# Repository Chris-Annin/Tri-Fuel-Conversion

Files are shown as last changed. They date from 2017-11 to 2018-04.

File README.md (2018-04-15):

# Tri-Fuel-Conversion
open source instructions and 3D print models to convert your generator to run on natural gas or propane

This project includes:

- Bill of materials and instructions
- CAD files to 3D print bracket and carburetor adapter

(https://youtu.be/Tu0BFD9ouBQ)

Overview: [Video](https://youtu.be/Tu0BFD9ouBQ)

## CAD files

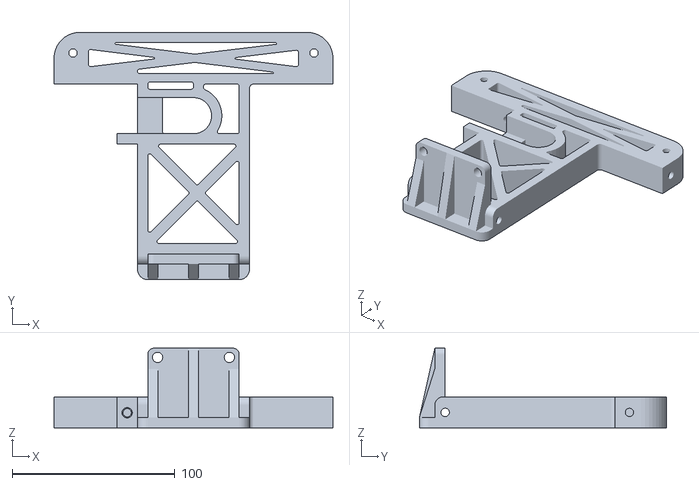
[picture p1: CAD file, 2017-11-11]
Mounting Bracket.STL
171.4 x 152.0 x 49.0

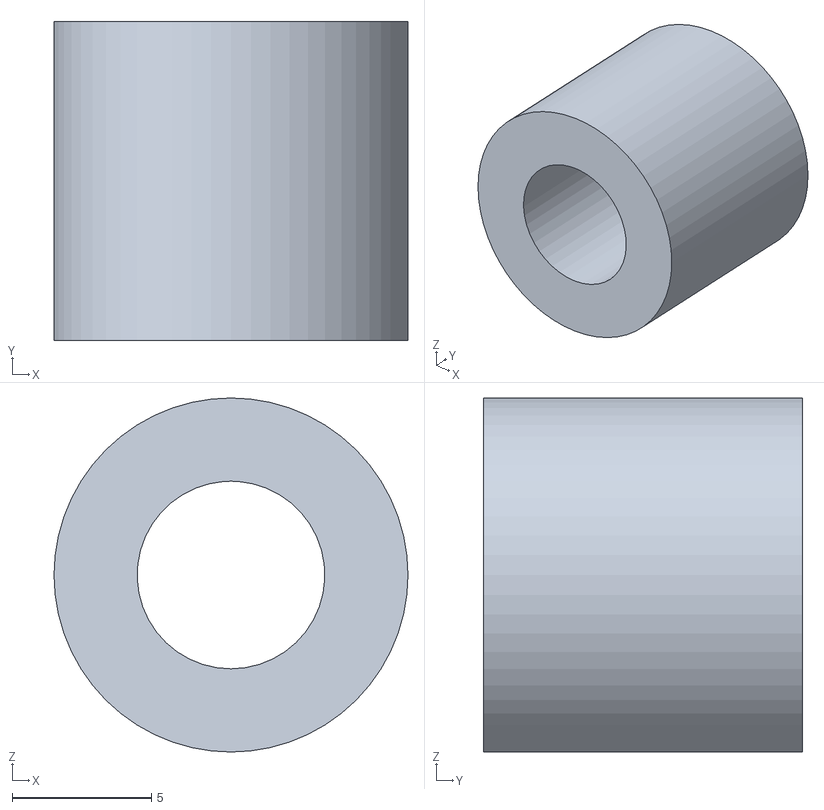
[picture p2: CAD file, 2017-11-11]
Lever Spacer.STL
12.7 x 11.4 x 12.7

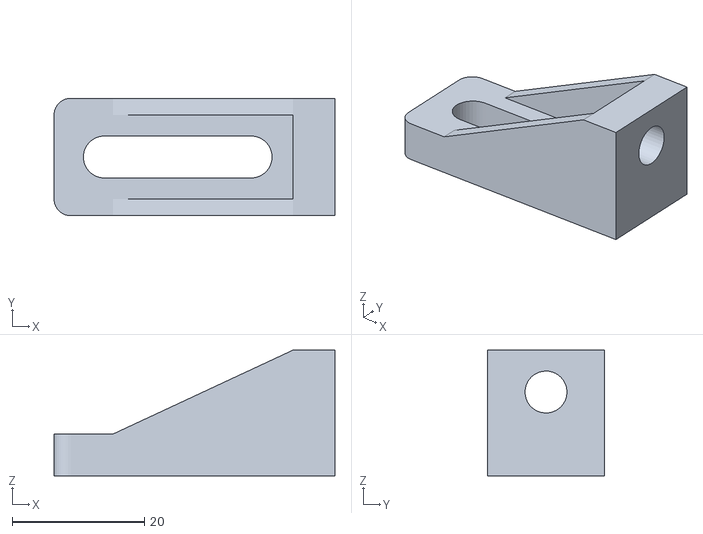
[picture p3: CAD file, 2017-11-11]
Foot.STL
42.5 x 17.8 x 19.1

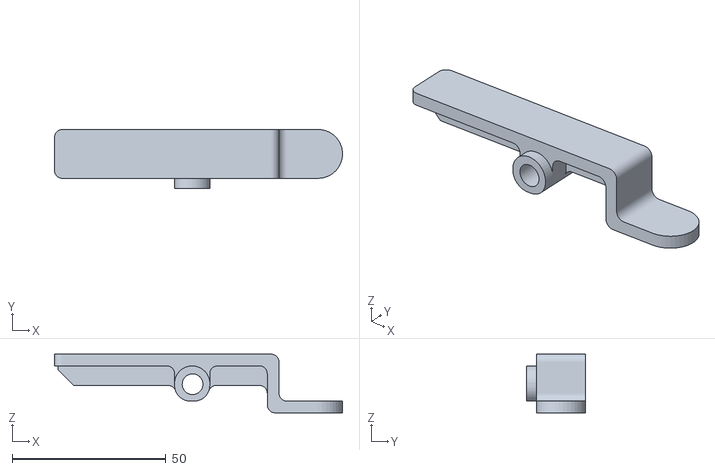
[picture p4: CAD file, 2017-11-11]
Lever.STL
93.5 x 19.2 x 19.1

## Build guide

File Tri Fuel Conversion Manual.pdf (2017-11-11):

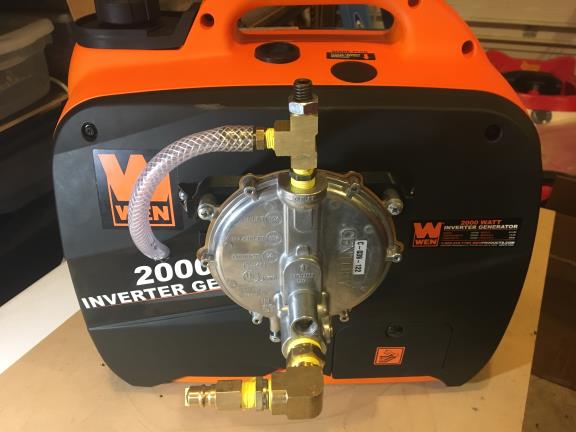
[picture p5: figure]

# Tri Fuel Conversion Manual

### - WARNING

- Never use a generator inside homes, garages,

### crawlspaces, or other partly enclosed areas. Deadly levels of carbon monoxide can build up in these areas. Using a fan or opening windows and doors

does NOT supply enough fresh air.

### - ONLY use a generator outdoors and far away from open windows, doors, and vents. Make sure to direct the generator's exhaust away from these openings because they can pull in generator

exhaust.

### - The generator must be at least 20 ft away from your

home.

- Before making any connections make sure you identify and eliminate all sources of ignition where natural gas may be vented, recognizing that natural gas is lighter than air and will rise. Sources of ignition include: - Standing pilots - Open flames - Cigarettes and other smoking products - Electric light switches and appliances - Motorized equipment and vehicles - Temperatures above 1,100 degrees Fahrenheit - Anything that may cause a spark - Use natural gas detection equipment during all natural gas or propane connection operations to prevent natural gas from accumulating and creating a combustible or hazardous atmosphere. DO NOT rely on your sense of smell alone to be alerted the

presence of natural gas.

# Bill of Materials

### ITEMS FROM AMAZON:

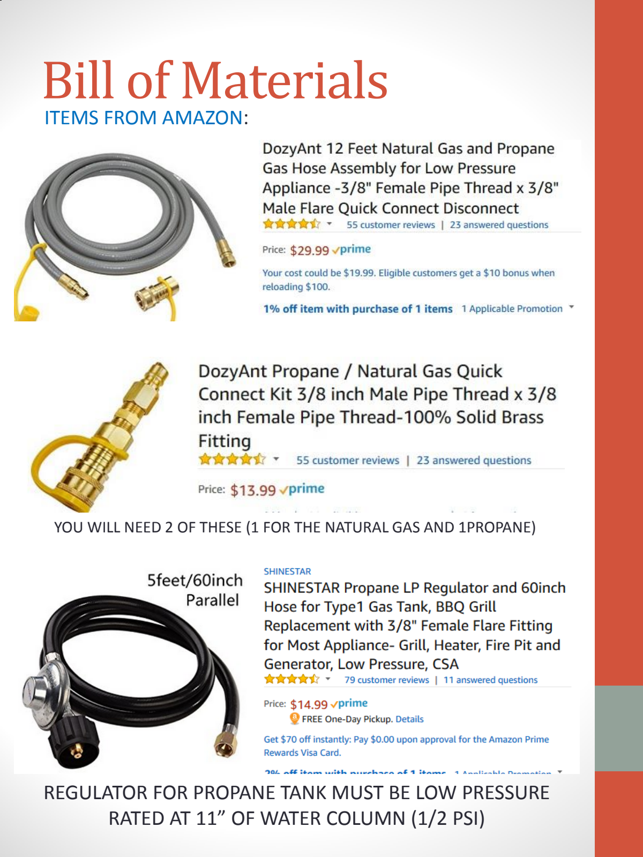
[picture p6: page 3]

YOU WILL NEED 2 OF THESE (1 FOR THE NATURAL GAS AND 1PROPANE)

### REGULATOR FOR PROPANE TANK MUST BE LOW PRESSURE RATED AT 11” OF WATER COLUMN (1/2 PSI)

### ITEMS FROM EBAY:

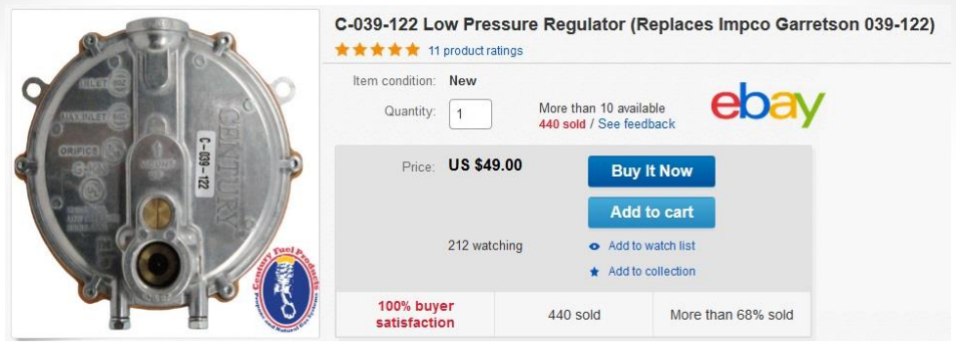
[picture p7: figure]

### ITEMS FROM HARDWARE STORE – GENERATOR FITTINGS:

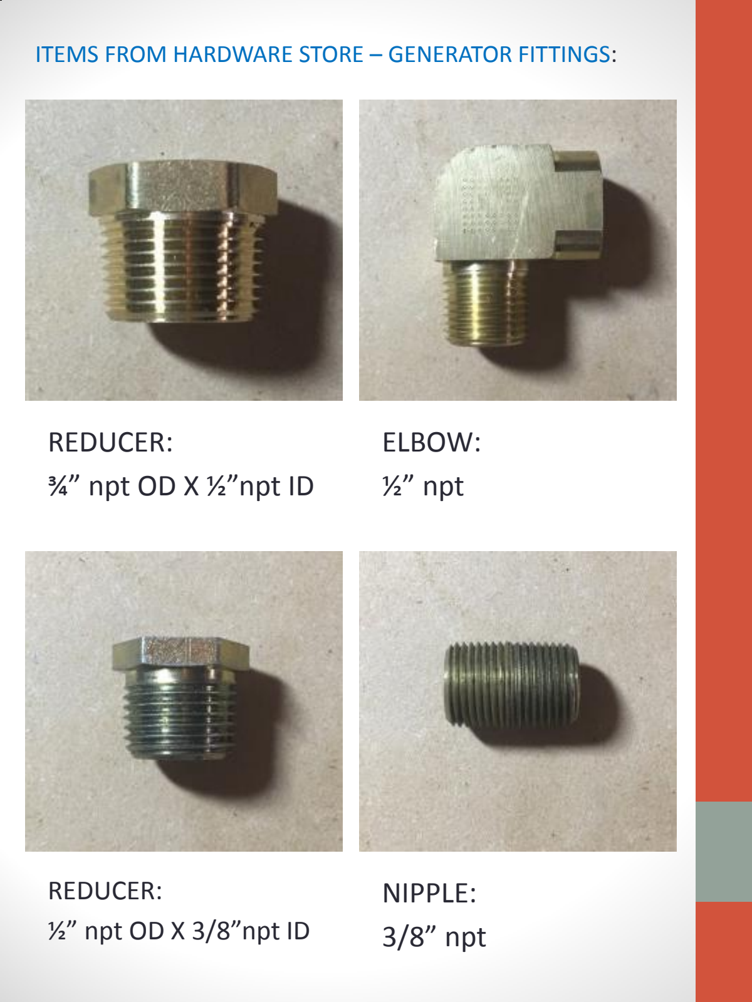
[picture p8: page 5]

## REDUCER: ¾” npt OD X ½”npt ID

## ELBOW: ½” npt

## REDUCER: ½” npt OD X 3/8”npt ID

## NIPPLE: 3/8” npt

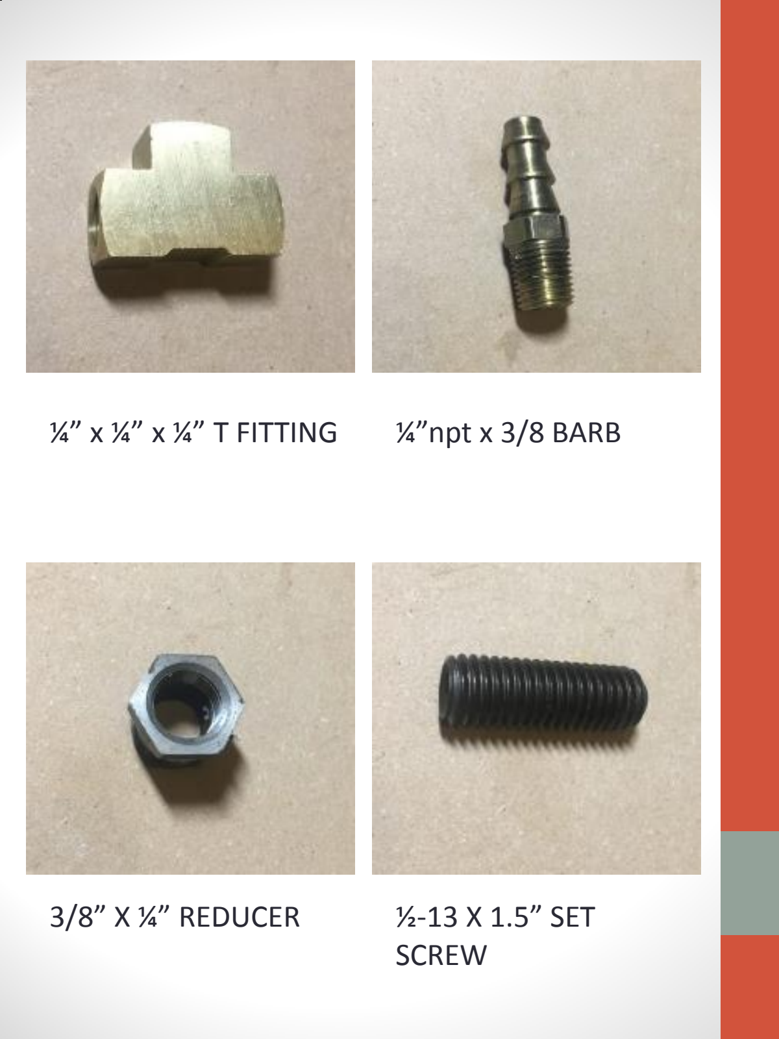
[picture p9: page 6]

3/8” X ¼” REDUCER | ½-13 X 1.5” SET SCREW
¼” x ¼” x ¼” T FITTING | ¼”npt x 3/8 BARB

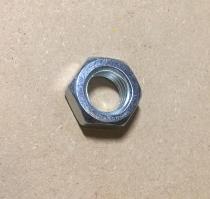
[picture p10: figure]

## ½-13 JAM NUT

## ¼” npt NIPPLE

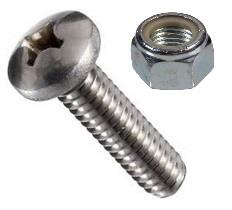
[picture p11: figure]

¼” x 1.75” machine screws (x1) ¼” x .5” machine screws (x8) ¼” X 1” machine screws (x2) ¼” nylon lock nuts (x4)

### ITEMS FROM HARDWARE STORE – NATURAL GAS SUPPLY:

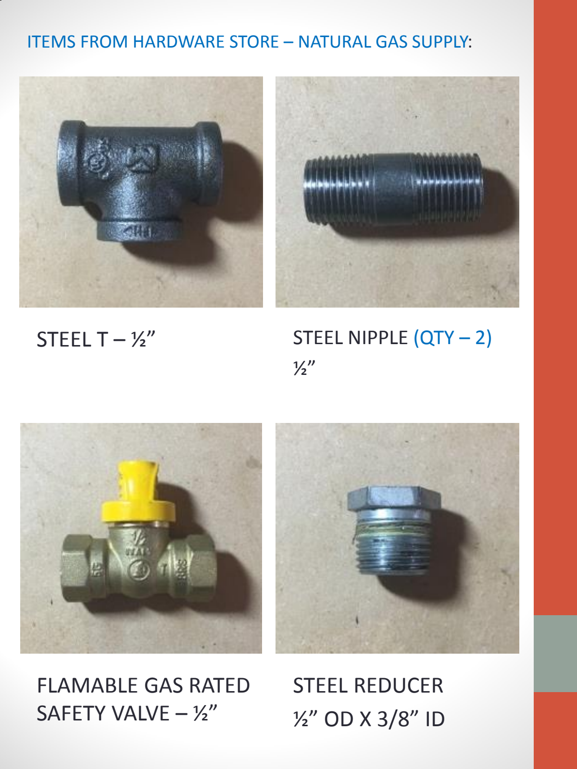
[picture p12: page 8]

STEEL T – ½” | STEEL NIPPLE (QTY – 2) ½”

## FLAMABLE GAS RATED SAFETY VALVE – ½”

## STEEL REDUCER ½” OD X 3/8” ID

## STEEL NIPPLE:

3/8”

## GAS RATED TEFLON TAPE

## FLARE FITTING: 3/8” FLARE X 3/8” npt

### ITEMS FROM HARDWARE STORE – PROPANE SUPPLY:

### 3D PRINTED PARTS

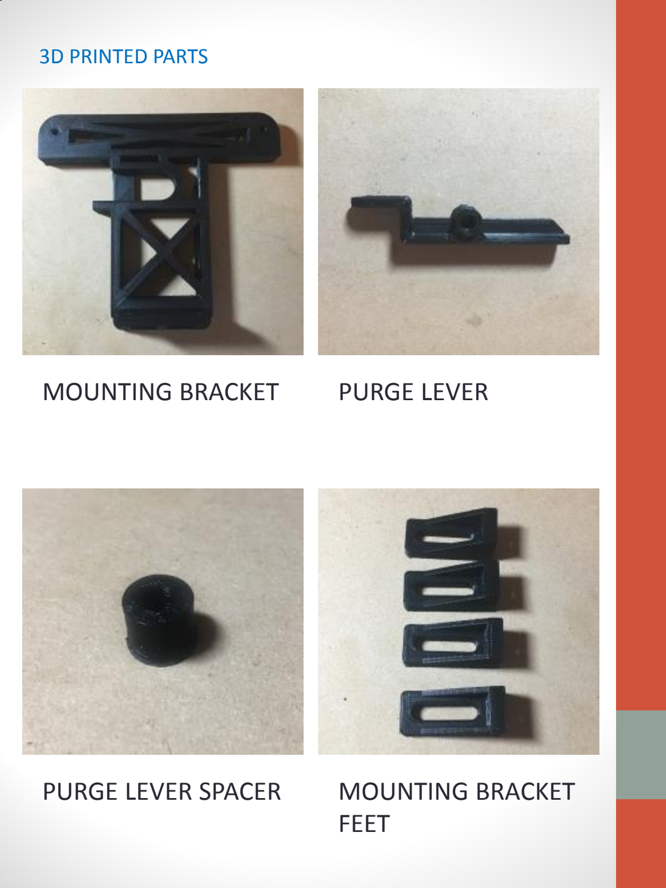
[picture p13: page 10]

MOUNTING BRACKET | PURGE LEVER
PURGE LEVER SPACER | MOUNTING BRACKET FEET

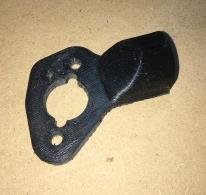
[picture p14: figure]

## CARBURATOR GAS ADAPTER

# Assembly

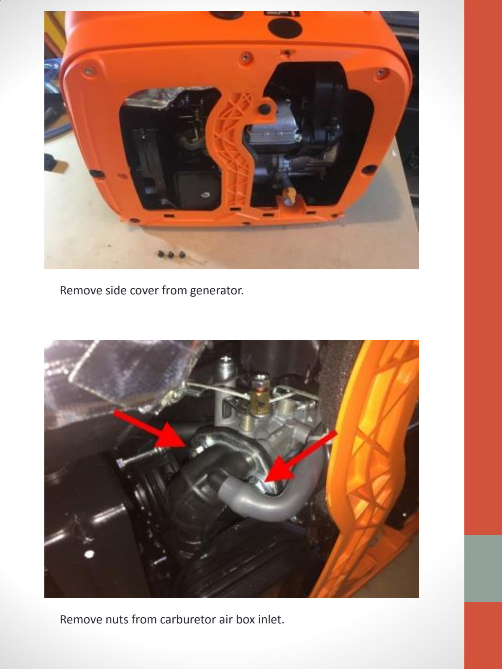
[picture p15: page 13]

Remove side cover from generator.

Remove nuts from carburetor air box inlet.

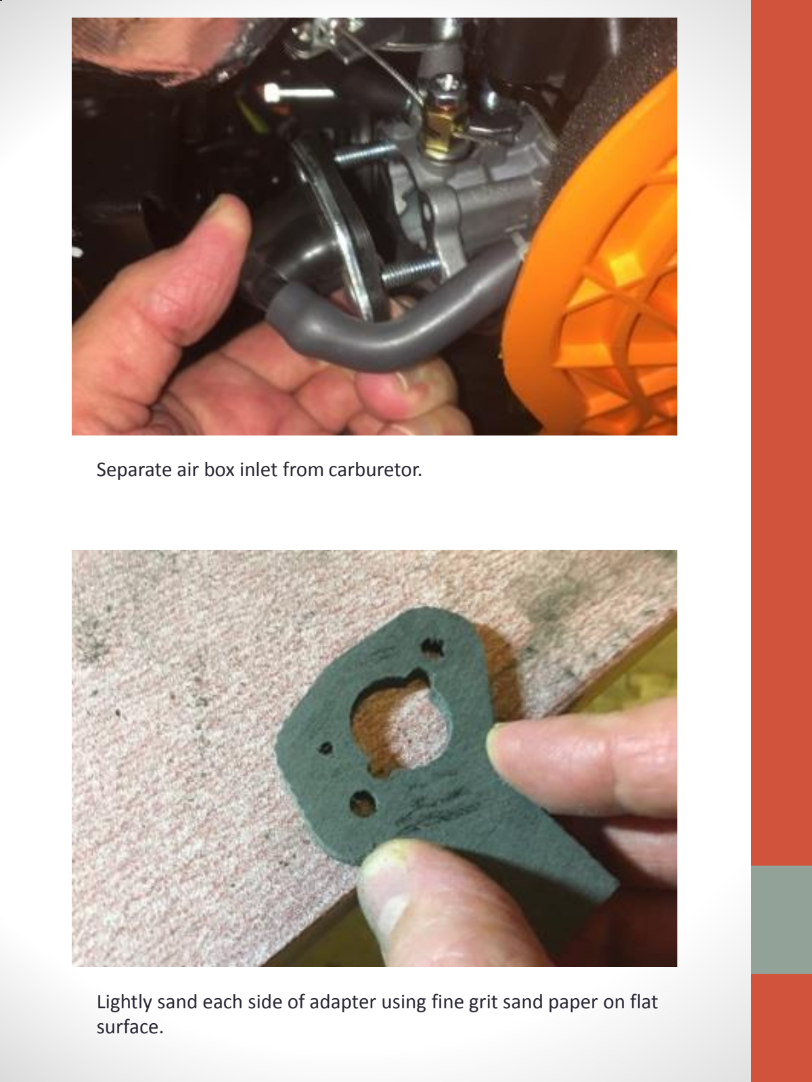
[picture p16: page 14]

Separate air box inlet from carburetor.

Lightly sand each side of adapter using fine grit sand paper on flat surface.

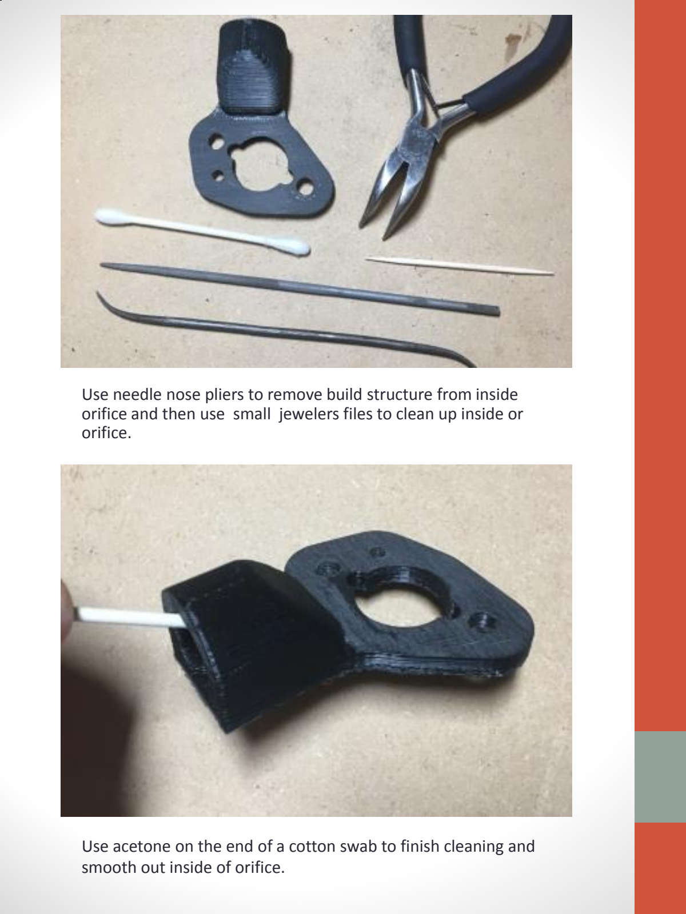
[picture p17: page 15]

Use needle nose pliers to remove build structure from inside orifice and then use small jewelers files to clean up inside or orifice.

Use acetone on the end of a cotton swab to finish cleaning and smooth out inside of orifice.

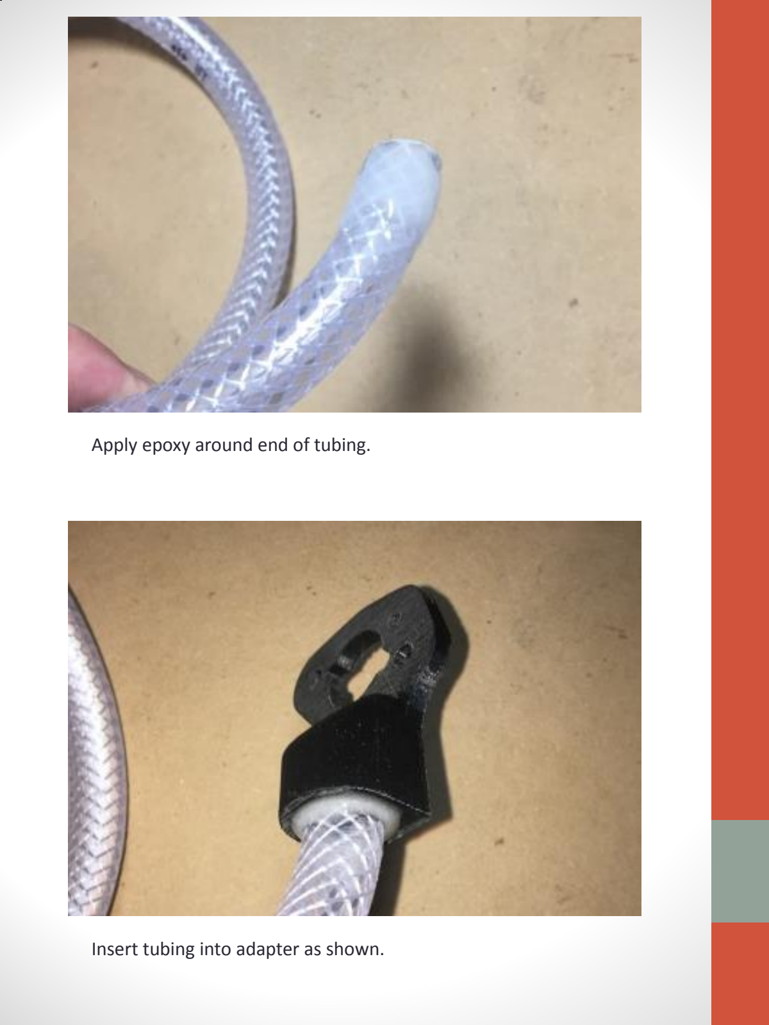
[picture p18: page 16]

Apply epoxy around end of tubing.

Insert tubing into adapter as shown.

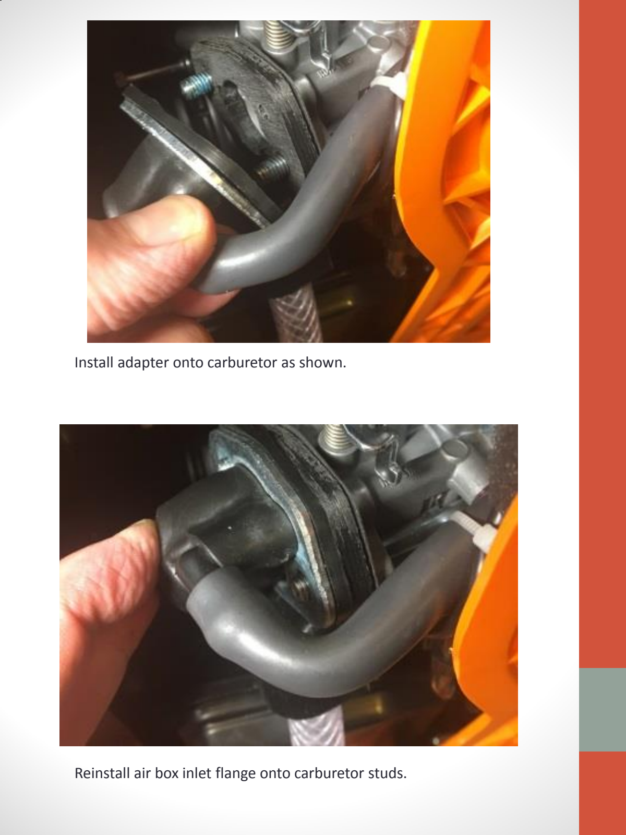
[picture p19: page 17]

Install adapter onto carburetor as shown.

Reinstall air box inlet flange onto carburetor studs.

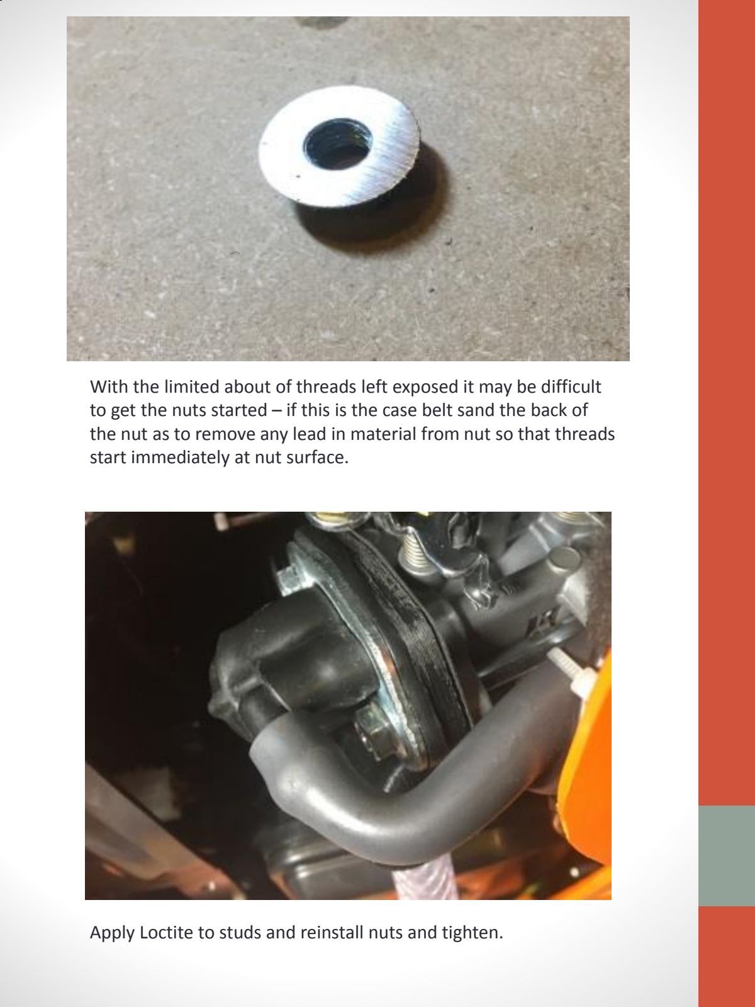
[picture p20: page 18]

With the limited about of threads left exposed it may be difficult to get the nuts started – if this is the case belt sand the back of the nut as to remove any lead in material from nut so that threads start immediately at nut surface.

Apply Loctite to studs and reinstall nuts and tighten.

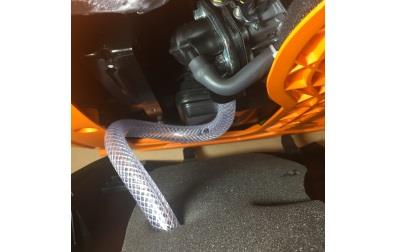
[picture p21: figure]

Drill ¼” hole in cover, run ¼” fuel line through the hole as shown then reinstall side cover.

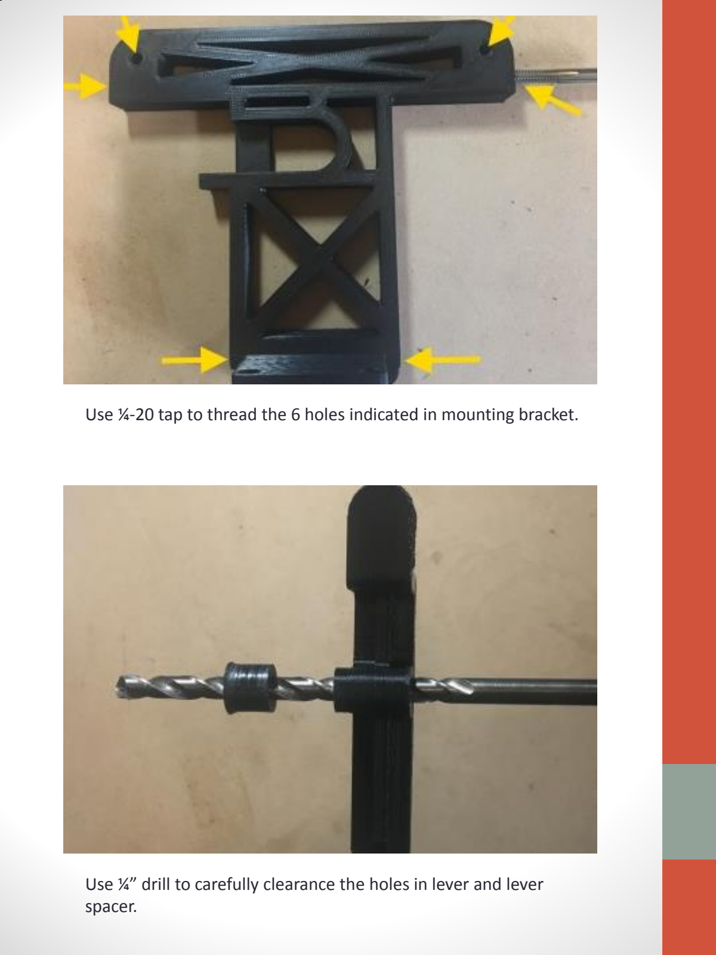
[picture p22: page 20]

Use ¼-20 tap to thread the 6 holes indicated in mounting bracket.

Use ¼” drill to carefully clearance the holes in lever and lever spacer.

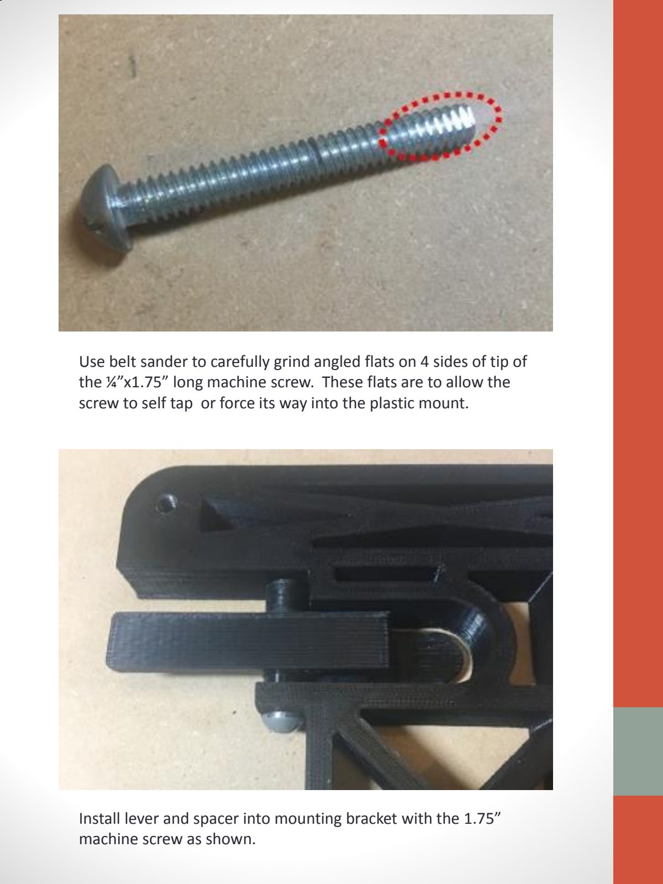
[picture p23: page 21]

Use belt sander to carefully grind angled flats on 4 sides of tip of the ¼”x1.75” long machine screw. These flats are to allow the screw to self tap or force its way into the plastic mount.

Install lever and spacer into mounting bracket with the 1.75” machine screw as shown.

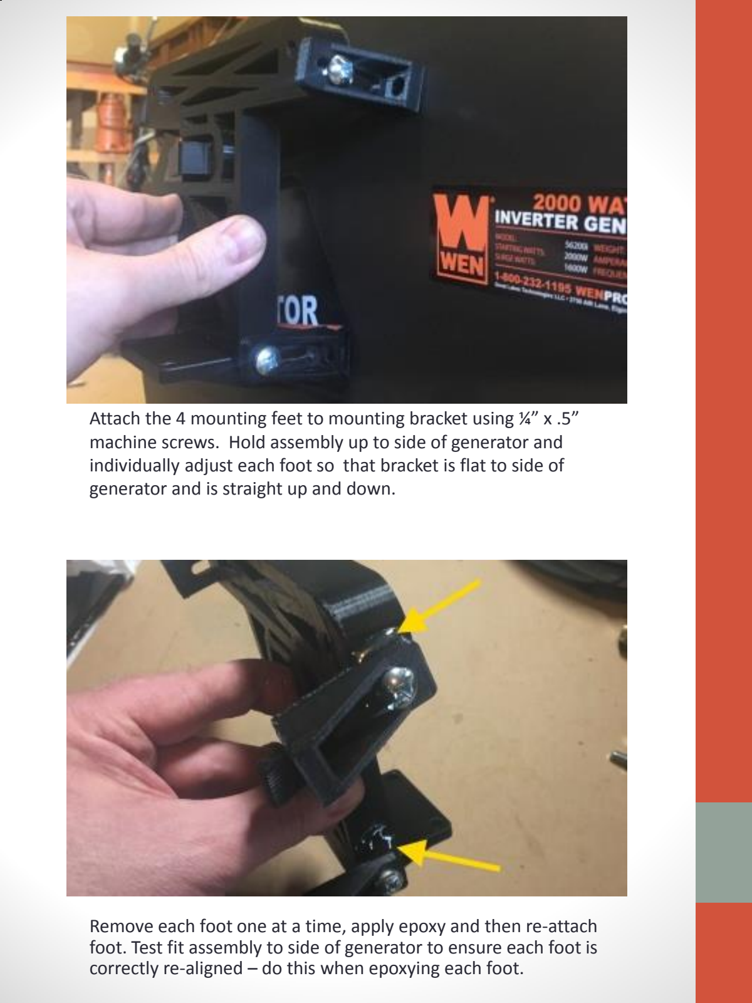
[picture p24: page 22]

Attach the 4 mounting feet to mounting bracket using ¼” x .5” machine screws. Hold assembly up to side of generator and individually adjust each foot so that bracket is flat to side of generator and is straight up and down.

Remove each foot one at a time, apply epoxy and then re-attach foot. Test fit assembly to side of generator to ensure each foot is correctly re-aligned – do this when epoxying each foot.

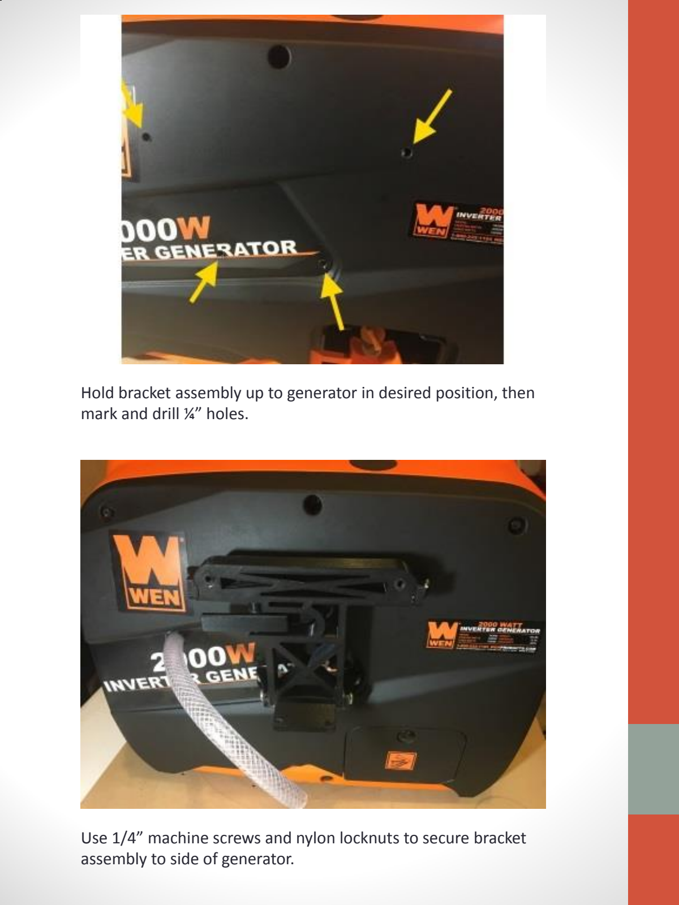
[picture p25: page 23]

Hold bracket assembly up to generator in desired position, then mark and drill ¼” holes.

Use 1/4” machine screws and nylon locknuts to secure bracket assembly to side of generator.

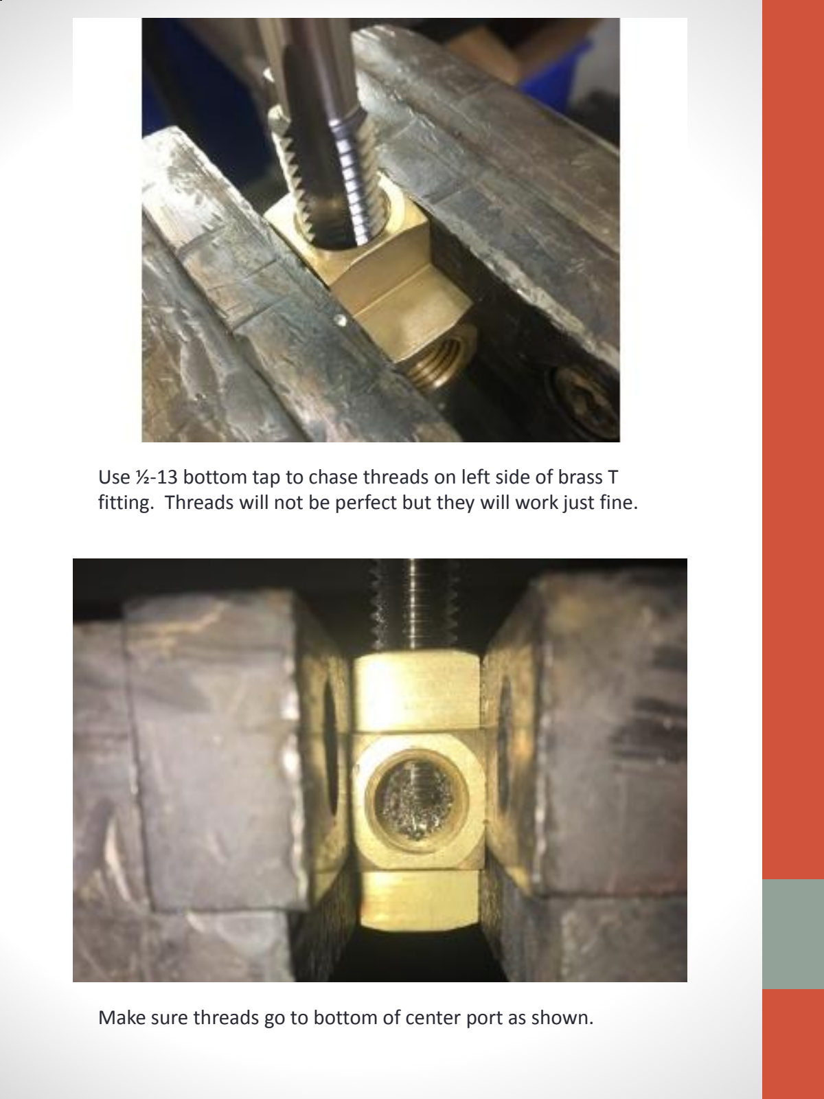
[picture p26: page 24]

Use ½-13 bottom tap to chase threads on left side of brass T fitting. Threads will not be perfect but they will work just fine.

Make sure threads go to bottom of center port as shown.

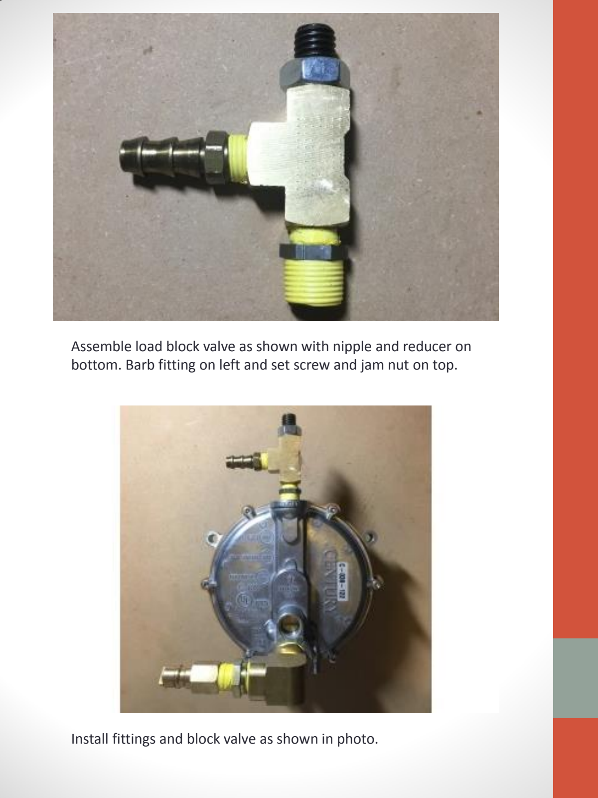
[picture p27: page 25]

Assemble load block valve as shown with nipple and reducer on bottom. Barb fitting on left and set screw and jam nut on top.

Install fittings and block valve as shown in photo.

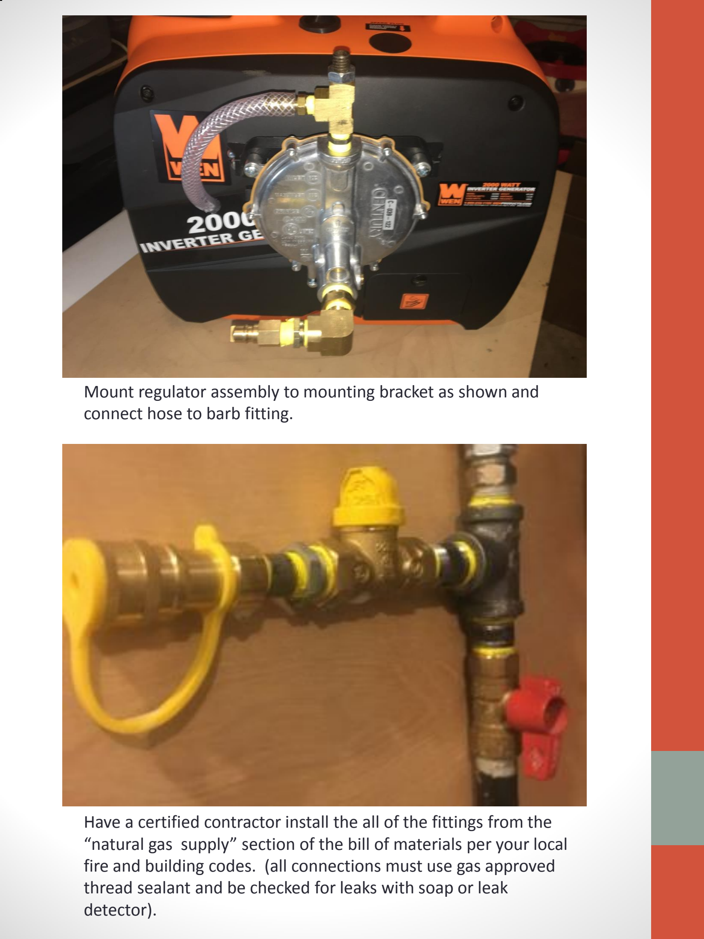
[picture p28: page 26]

Mount regulator assembly to mounting bracket as shown and connect hose to barb fitting.

Have a certified contractor install the all of the fittings from the “natural gas supply” section of the bill of materials per your local fire and building codes. (all connections must use gas approved thread sealant and be checked for leaks with soap or leak detector).

WARNING
Never use a generator inside homes, garages, crawlspaces, or other partly enclosed areas. Deadly levels of carbon monoxide can build up in these areas. Using a fan or opening windows and doors does NOT supply enough fresh air.
ONLY use a generator outdoors and far away from open windows, doors, and vents. Make sure to direct the generator's exhaust away from these openings because they can pull in generator exhaust.
The generator must be at least 20 ft away from your home. Before making any connections make sure you identify and eliminate all sources of ignition where natural gas may be vented, recognizing that natural gas is lighter than air and will rise. Sources of ignition include:
Standing pilots
Open flames
Cigarettes and other smoking products Electric light switches and appliances Motorized equipment and vehicles
Temperatures above 1,100 degrees Fahrenheit
Anything that may cause a spark
Use natural gas detection equipment during all natural gas connection or propane operations to prevent natural gas from accumulating and creating a combustible or hazardous atmosphere. DO NOT rely on your sense of smell alone to be alerted the presence of natural gas.

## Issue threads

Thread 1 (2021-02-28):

Adapter warping and cracking

2020Phattony, 2021-02-28:
Hi Chris,

Appreciate the work on this and providing the files.  I had the adapter printed using ASA 0.01" resolution, installed it, and had it [running for a few minutes](https://phattony.box.com/s/sh05sgvwaznulaxh6l7tb089qi285joj).

However, a few days later I tried running it on NG, noticed the engine couldn't run steadily with eco mode on.  Previously I had it running with eco off.

I took it apart and noticed that the adapter was warped and cracked, which is probably why the generator was struggling.

I was curious if you noticed anything similar or maybe the variance is in the resolution of your print and filament choice (ABS I believe?).

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

Any revisions to the adapter?

Thanks,

Tony

Chris-Annin, 2021-02-28:
Hello, I haven't used ASA myself but I understand it's supposed to be a
superior material.  I have used ABS and I printed at .2mm layer height.  I
know that I have had marginal results with ABS unless using a fully
enclosed printer. I'm not an expert on printing but with the open frame
printer I have now I would go with PETG.  Hope that helps.

On Sun, Feb 28, 2021, 11:05 AM 2020Phattony <notifications@github.com>
wrote:

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

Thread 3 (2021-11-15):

Tubing from adapter to regulator missing from parts list

stevebartlow, 2021-11-15:
Hey Chris, it looks like the parts list is missing the tubing from the adapter to the regulator.  Is the spec for that listed somewhere?  I didn't catch it in the video or in any of the instructions.

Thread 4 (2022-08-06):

You don't need the Load Block

Ergonomicmike, 2022-08-06:
First, thanks for the video and this github. It gave me the impetus/'courage' to try this conversion for myself on my WEN 56235i.

After doing additional research on the 'net, I found that you do not need the Load Block.

Instead - and arguably better - you can adjust the pressure at the carburetor directly. (Better because the Regulator works exactly as intended, regulating the pressure directly without an indirect middle man Load Block. And better because it saves a lot of time not having to make a Load Block.)

To obtain access to the adjustment, you have to remove a plug from the shaft that is located above the input hole to the regulator. Once the plug is out, you'll see a similar brass screw in the shaft. That is the adjustment for setting the pressure of the regulator. (My plug was very tight. It would not come out, even when using an Impact Wrench. (I don't know if they peen the threads at the factor to prevent the plug from backing out.) I had to drill into it and then use a screw extractor to remove it.)

Here's a video showing the adjustment: youtube.com/watch?v=d8A-k-TUnwg
Jump to the 1 minute mark.

I found that the adjustment at load is very sensitive - less than a half turn making the difference between running smoothly at a load of 1400 Watts vs. hunting and then cutting out due to 'overload.' (I first adjusted the regulator with no load, so that the generator ran smoothly. And then I applied a load and adjust the regulator some more so that the generator ran smoothly again at load.) Screwing the plug "in," CW, is less gas. CCW is more gas. I was a few turns from full in.

And remember that Natural Gas does not have the energy density that gasoline has. So if your generator is rated for, say, 2000 Watts continuous when burning gasoline, don't expect 2000 W when using Natural Gas. (I have seen varying numbers on the 'net. But 80% of rated power seems nominal for NG.)

Next, you might not need the 3d printed adapter. Many ppl on the 'net are simply drilling a hole into their air filter box and pushing the tube (for gas) into the box. Not as elegant and perhaps not as responsive to load changes with all the volume in the air box acting as a buffer.  But I mention it for people who don't have a 3d printer and who need to run on NG in an emergency.

As it was, I remixed the 3d print and I made my adapter flange less thick so that the nuts could go on the carburetor studs without having to grind down the OEM nuts. I also used PETG filament to make the part, which I thought was obviously necessary since PLA doesn't handle heat very well.

Last, there are two ports on each of the lower sides of the Regulator. (At 8 and 4 o'clock.) The photo of your Regulator, shown in your pdf, does not show these ports. But I'm thinking that they must be there. (Mine have bosses that protrude a bit past the main shell.) Anyway, one guy in an Amazon Review said that the ports were for pilot light plumbing and that the ports need to be plugged. That is incorrect.

The ports need to remain open, as they let air into the Regulator. Jump to 4:28 in this video: youtube.com/watch?v=CfM6D65MC_w
(You can feel air being sucked into these ports when your generator is running.)

So if your Regulator came with red plastic inserts/keepers in these two holes, remove them to let the Regulator breath.

Hope this helps.
